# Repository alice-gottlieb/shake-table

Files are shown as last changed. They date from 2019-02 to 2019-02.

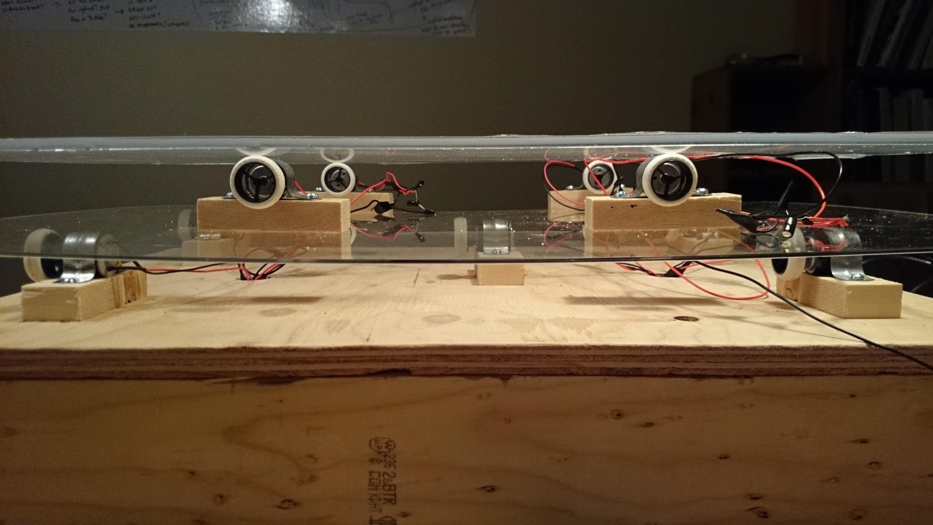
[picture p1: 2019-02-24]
picturesAndVideos/XY-FullBuild.JPG

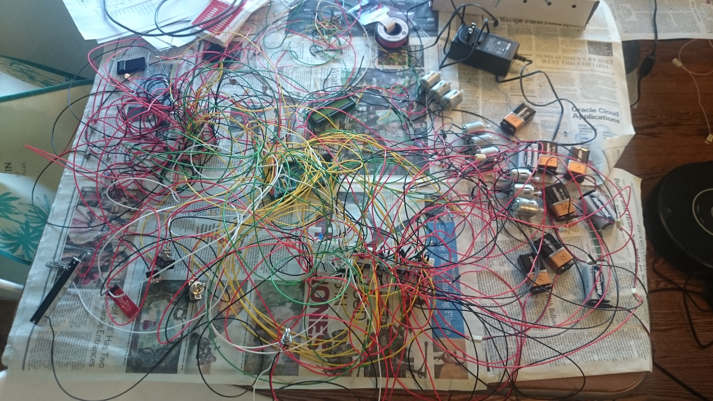
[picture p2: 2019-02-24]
picturesAndVideos/AllWiredTogether.JPG

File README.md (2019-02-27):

# shake-table
Circuit diagram and Arduino Programs to build and operate an earthquake-simulating shake table. <br>
Built using Arudino Mega 2560 Rev 3 <br>
Feature list:
* Movement in X, Y, and Z axes
* 10 DC motors
* 16 low-power vibrating motors for aftershock simulation
* Multiple potentiometers for active control of shake power 
* Readout via LCD display (not shown on circuit diagram, but supported in Arduino code), multicolored LEDs, and a variety of audio tones
* Real-time clock 
* Bluetooth connectivity

All code needed to operate shake table inside shakeTableOperationCode. Specific tests for debugging are inside testCode. Include [RTC-Lib](https://github.com/adafruit/RTClib) to operate real-time clock <br>

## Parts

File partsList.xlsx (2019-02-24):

Part Name and Quantity | URL | Unit Price | Total Price
1x Arduino Mega 2560 Rev3 Microcontroller | https://www.sparkfun.com/products/11061 | $45.95 | $45.95
17x vibration motors | https://www.sparkfun.com/products/8449 | $4.46 | $75.82
6x SN754410 H-Bridges | https://www.sparkfun.com/products/315 | $2.35 | $14.10
1x Bluetooth Mate Silver | https://www.sparkfun.com/products/12577 | $24.95 | $24.95
11x motors | https://www.sparkfun.com/products/11696 | $1.76 | $19.36
5x 9v batteries | https://www.sparkfun.com/products/10218 | $1.95 | $9.75
1x 110v AC-to-9v DC adapter | https://www.sparkfun.com/products/12889 | $5.95 | $5.95
11x 100uF capacitors | https://www.sparkfun.com/products/96 | $0.32 | $3.52
11x 10uF capacitors | https://www.sparkfun.com/products/523 | $0.41 | $4.51
4x 74HC595 SIPO Shift Registers | https://www.sparkfun.com/products/733 | $1.50 | $6.00
11x NPN BJN Transistors | https://www.sparkfun.com/products/12852 | $0.45 | $4.95
2x rotary potentiometers (linear sweep) | https://www.sparkfun.com/products/9939 | $0.95 | $1.90
2x rotary potentiometers (logarithmic sweep) | https://www.sparkfun.com/products/9940 | $0.95 | $1.90
2x linear potentiometers (linear sweep) | https://www.sparkfun.com/products/9119 | $2.95 | $5.90
1x DS1307 RTC Breakout Board | https://www.sparkfun.com/products/12708 | $14.95 | $14.95
1x resistor kit | https://www.sparkfun.com/products/10969 | $7.95 | $7.95
15x green LEDs (common cathode) | https://www.sparkfun.com/products/9650 | $0.32 | $4.80
5x blue LEDs (common cathode) | https://www.sparkfun.com/products/11372 | $0.50 | $2.50
5x red LEDs (common cathode) | https://www.sparkfun.com/products/9590 | $0.35 | $1.75
2x RGD LEDs (common cathode) | https://www.sparkfun.com/products/105 | $1.95 | $3.90
2x switches | https://www.sparkfun.com/products/9276 | $1.95 | $3.90
1x 16x2 LCD screens with RGB LED backlight | https://www.sparkfun.com/products/10862 | $14.95 | $14.95
1x assorted wires | http://www.amazon.com/Electronix-Express-Hook-Wire-Stranded/dp/B00B4ZQ3L0 | $20.00 | $20.00
2x female headers | https://www.sparkfun.com/products/115 | $1.50 | $3.00
1x storage bin | : http://www.amazon.com/Akro-Mils-20-Inch-16-Inch-Hardware-Cabinet/dp/B003P2UOCO | $26.71 | $26.71
10x 9v battery holders | https://www.sparkfun.com/products/91 | $1.13 | $11.30
 |  |  | Total:
 |  |  | $340.27

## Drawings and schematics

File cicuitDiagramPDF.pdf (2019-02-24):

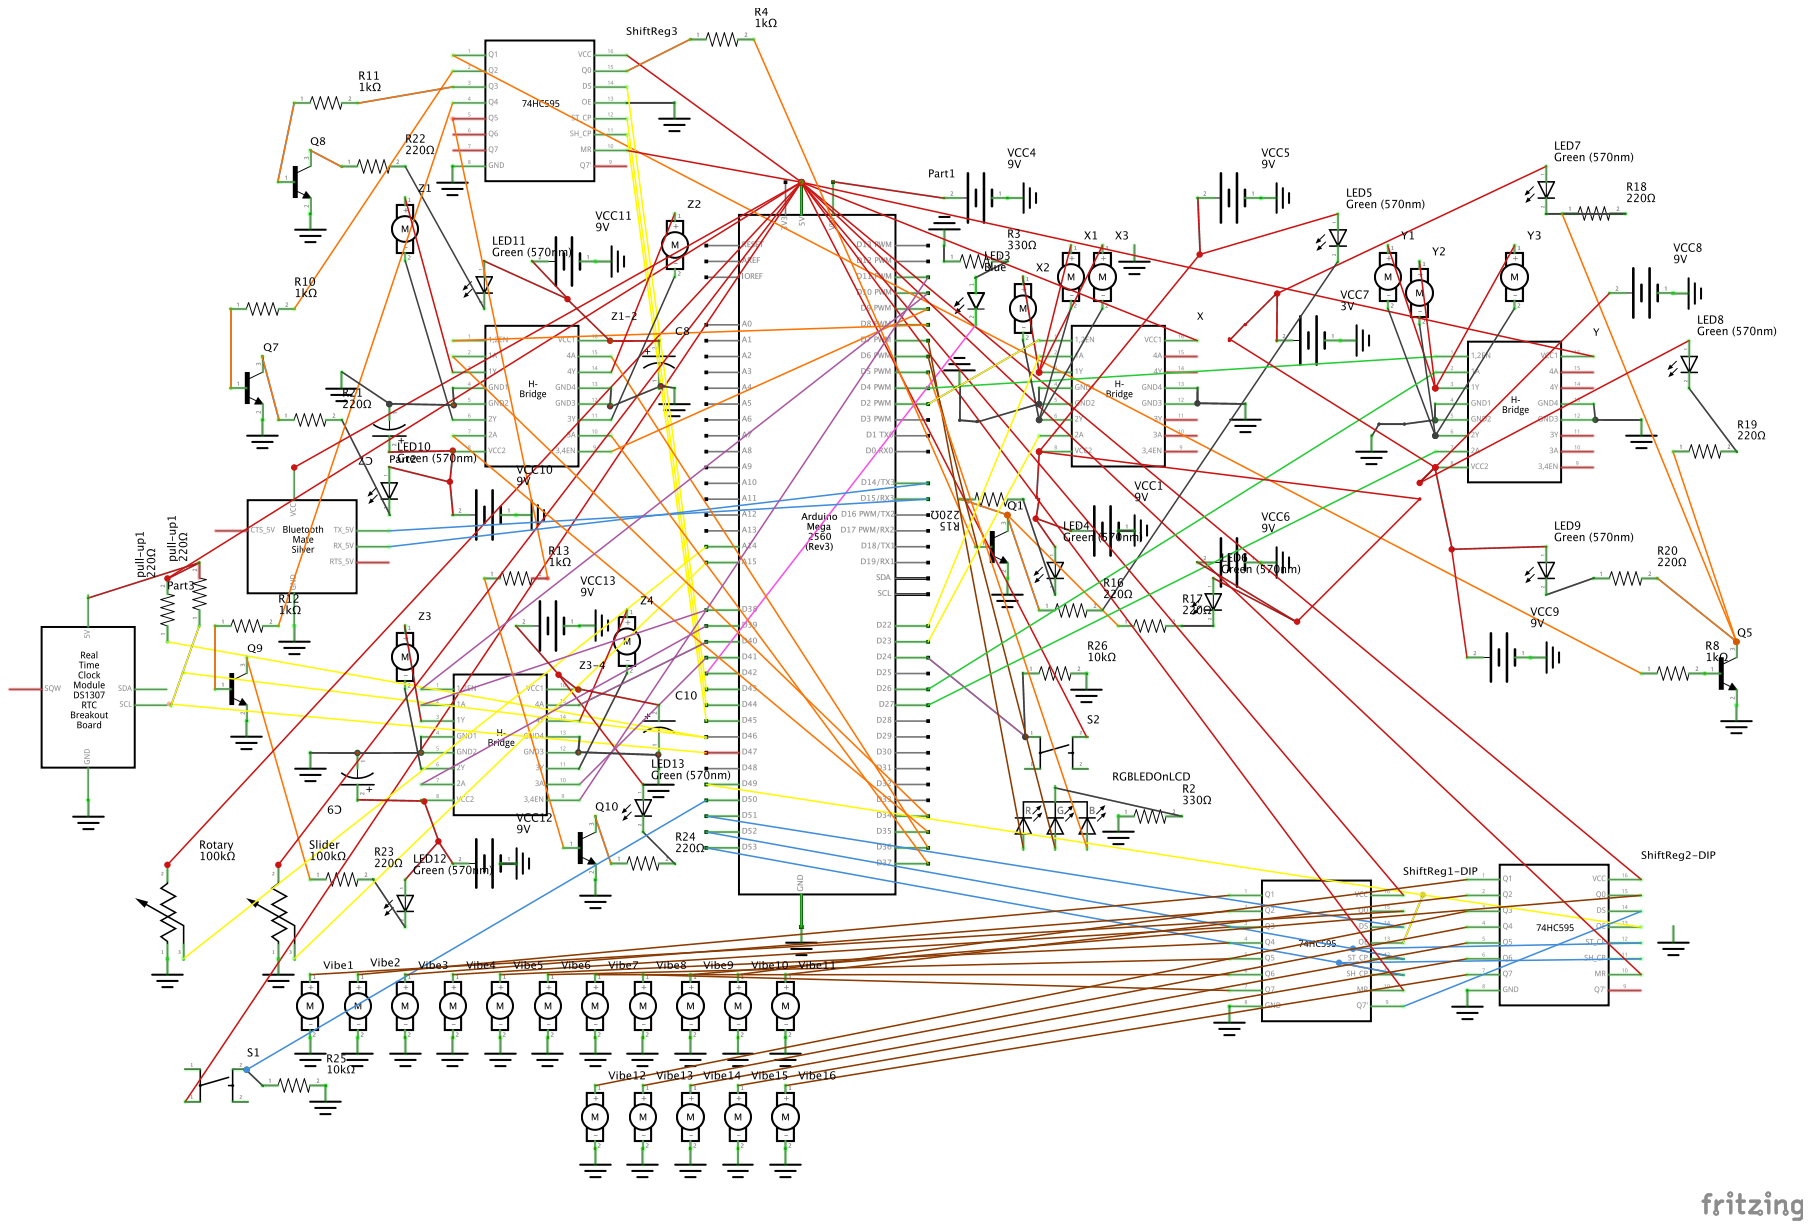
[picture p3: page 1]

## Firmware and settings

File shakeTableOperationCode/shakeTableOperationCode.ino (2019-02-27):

#include <LiquidCrystal.h>
#include <Wire.h>
//#include "RTClib.h"

/*
All functions needed to run Shake table.
Diagnostics will run automatically, other functions can be used as needed depending on settings needed.
Include RTClib to operate real-time clock
Notes:
clockwise = switch1 HIGH and switc2 LOW
countercloskwise = switch1 LOW and switch2 HIGH
clockwise is up
*/
//LiquidCrystal lcd (44, 45, 46, 47, 48, 49);
//pin numbers
byte xMotorEN = 2; //pwm
byte yMotorEN = 4; //pwm
byte z1MotorEN = 8; //pwm
byte z2MotorEN = 9; //pwm
byte z3MotorEN = 10; //pwm
byte z4MotorEN = 11; //pwm
byte lcdGreenBacklight = 12; //pwm
byte lcdRedBacklight = 13; //pwm
byte bluetoothTX = 14; //AKA TX3
byte bluetoothRX = 15; //AKA RX3
byte lcdTX = 16;
byte xMotorSwitch1  = 22;
byte xMotorSwitch2 = 23;
byte onOffSwitch = 24;
byte yMotorSwitch1 = 26;
byte yMotorSwitch2 = 27;
byte z1MotorSwitch1 = 34;
byte z1MotorSwitch2 = 35;
byte z2MotorSwitch1 = 36;
byte z2MotorSwitch2 = 37;
byte z3MotorSwitch1 = 38;
byte z3MotorSwitch2 = 39;
byte z4MotorSwitch1 = 40;
byte z4MotorSwitch2 = 41;
byte bluetoothStatusLED = 42;
byte bluetoothOnOffSwitch = 50; //digital input
byte vibeMotorShiftRegisterData = 51; //this is daisy-chained to another shift register, so there are 2 bytes of data to be sent
byte vibeMotorShiftRegisterLatch = 52;
byte vibeMotorShiftRegisterClock = 53;
byte batteryTesterShiftRegisterData = 43;
byte batteryTesterShiftRegisterLatch = 44;
byte batteryTesterShiftRegisterClock = 45;
//byte z3BatteryTester = A3;
//byte RTCData = 46;
//byte RTCClock = 47; 
//byte z4BatteryTester = A6;
byte rotaryPot = A14; //analog input
byte linearPot = A15; //analog input
//RTC_DS1307 RTC;

/*
Z  motor definitions:
motors deifind looking from behind lcd readout screen
z1Motor: bottom right corner
z2Motor: bottom left corner
z3Motor: top center
code definitions:
code 1: entire right side (z1) up, entire left side (z2) down
code 2: entire left side (z2) up, entire right side (z1) down
code 3: entire bottom side (z1, z3) up, entire top side (z2, z4) down
code 4: entire top side (z2, z4) up, entire bottom side (z1, z3) down
code 5: bottom right corner (z1) up, top left corner (z3) down
code 6: top left corner (z3) up, bottom right corner (z1) down
code 7: top right corner (z2) up, bottom left corner (z4) down
code 8: bottom left corner (z4) up, top right corner (z2) down
any other code: turns off all motors
*/

void setup(){
  //setup of pins
  for(byte pinNum = 0; pinNum < 54; pinNum++){
    pinMode(pinNum, OUTPUT);
  }
  pinMode(bluetoothOnOffSwitch, INPUT);
  pinMode(batteryTesterShiftRegisterData, OUTPUT);
  pinMode(batteryTesterShiftRegisterLatch, OUTPUT);
  pinMode(batteryTesterShiftRegisterClock, OUTPUT);
  pinMode(bluetoothRX, INPUT);
  pinMode(rotaryPot, INPUT);
  pinMode(linearPot, INPUT);
  //start LCD Display
  digitalWrite(lcdTX, HIGH);
  Serial2.begin(9600);
  delay(100);
  Serial2.write(24); //turn on w/ cursor + no blink
  Serial2.write(12); //clear
  delay(5);
  Serial2.print("Hello There!");
  Serial2.write(13); //carriage return
  /*for(int i = 0; i < 5; i++){
    DateTime dateTime = RTC.now();
    String year = String(dateTime.year(), DEC);
    String month = String(dateTime.month(), DEC);
    String day = String(dateTime.day(), DEC);
    String hour = String(dateTime.hour(), DEC);
    String minute = String(dateTime.minute(), DEC);
    String second = String(dateTime.second(), DEC);
    String date = month + "/" + day + "/" + year;
    String time = hour + ":" + minute + ":" + second;
    Serial2.print(time);
    lineErase(1);
    delay(1000);
  }*/
  Serial2.print("Diagnostics ...");
  diagnostics();
}

void loop(){
  
}

void diagnostics(){
  //lcd screen diags
  Serial2.write(12); 
  delay(5);
  Serial2.print("Diagnostics ...");
  Serial2.write(13); //cariage return
  //battery diags
  Serial2.print("Battery Diags");
  shiftOut(batteryTesterShiftRegisterData, batteryTesterShiftRegisterClock, LSBFIRST, B10000000);
  delay(500);
  shiftOut(batteryTesterShiftRegisterData, batteryTesterShiftRegisterClock, LSBFIRST, B01000000);
  delay(500);
  shiftOut(batteryTesterShiftRegisterData, batteryTesterShiftRegisterClock, LSBFIRST, B00100000);
  delay(500);
  shiftOut(batteryTesterShiftRegisterData, batteryTesterShiftRegisterClock, LSBFIRST, B00010000);
  delay(500);
  shiftOut(batteryTesterShiftRegisterData, batteryTesterShiftRegisterClock, LSBFIRST, B00001000);
  delay(500);
  shiftOut(batteryTesterShiftRegisterData, batteryTesterShiftRegisterClock, LSBFIRST, B00000100);
  delay(500);
  shiftOut(batteryTesterShiftRegisterData, batteryTesterShiftRegisterClock, LSBFIRST, B11111100);
  delay(500);
  shiftOut(batteryTesterShiftRegisterData, batteryTesterShiftRegisterClock, LSBFIRST, B00000000);
  //motor diags
  lineErase(1);
  Serial2.print("Motor Diags");
  moveXYMotors(100, true, true, 1000); //more x clockwise for 1 sec at speed 100
  moveXYMotors(100, true, false, 1000); //more x counter-clockwise for 1 sec at speed 100
  moveXYMotors(100, false, true, 1000); //more y clockwise for 1 sec at speed 100
  moveXYMotors(100, false, false, 1000); //more y counter-clockwise for 1 sec at speed 100
  /*for(byte n = 1; n <= 8; n++){ //loop through each case for Z
    moveZMotors(100, n, 1000); 
    delay(100);
  }*/
}

void moveXYMotors(double motorSpeed, boolean isX, boolean isClockwise, int time){ //speed is max 255, time is in milliseconds
  if(isX){
    if(isClockwise){
      //set to clockwise motion
      digitalWrite(xMotorSwitch1, HIGH);
      digitalWrite(xMotorSwitch2, LOW);  
    }
    else{
      //set to clockwise motion
      digitalWrite(xMotorSwitch1, LOW);
      digitalWrite(xMotorSwitch2, HIGH);  
    }
    //turn motors on
    for(int i = 0; i < 50; i++){
      analogWrite(xMotorEN, (motorSpeed*(i/50)));
      delay(time/50);
    }
    for(int i = 0; i < 50; i++){
      analogWrite(xMotorEN, (motorSpeed - (motorSpeed*(i/50))));
      delay(time/50);
    }
    //turn motors off
    analogWrite(xMotorEN, 0);
  }
    else{
    if(isClockwise){
      //set to clockwise motion
      digitalWrite(yMotorSwitch1, HIGH);
      digitalWrite(yMotorSwitch2, LOW);   
    }
    else{
      //set to clockwise motion
      digitalWrite(yMotorSwitch1, LOW);
      digitalWrite(yMotorSwitch2, HIGH);  
    }
    //turn motors on
    for(int i = 0; i < 50; i++){
      analogWrite(yMotorEN, (motorSpeed*(i/50)));
      delay(time/50);
    }
    for(int i = 0; i < 50; i++){
      analogWrite(yMotorEN, (motorSpeed - (motorSpeed*(i/50))));
      delay(time/50);
    }
    //turn motors off
    analogWrite(yMotorEN, 0);
  }
}

void moveXYMotors(double motorSpeed, boolean isX, boolean isClockwise, boolean isOn){ //speed is max 255, no time delay
  if(isOn){
    if(isX){
      if(isClockwise){
        //set to clockwise motion
        digitalWrite(xMotorSwitch1, HIGH);
        digitalWrite(xMotorSwitch2, LOW);  
      }
      else{
        //set to clockwise motion
        digitalWrite(xMotorSwitch1, LOW);
        digitalWrite(xMotorSwitch2, HIGH);   
      }
        //turn motors on
        analogWrite(xMotorEN, motorSpeed);
    }
    else{
      if(isClockwise){
        //set to clockwise motion
        digitalWrite(yMotorSwitch1, HIGH);
        digitalWrite(yMotorSwitch2, LOW);  
      }
      else{
        //set to clockwise motion
        digitalWrite(yMotorSwitch1, LOW);
        digitalWrite(yMotorSwitch2, HIGH);   
      }
      //turn motors on
      analogWrite(yMotorEN, motorSpeed);
    }
  }
  else{
    if(isX){
      analogWrite(xMotorEN, 0);
    }
    else{
      analogWrite(yMotorEN, 0);
    }
  }
}

void moveZMotors(double motorSpeed, byte code, int time){
  /*
  motor definitions:
  motors deifind looking from behind lcd readout screen
  z1Motor: bottom right corner
  z2Motor: top right corner
  z3Motor: top left corner
  z4Motor: bottom left corner
  code definitions:
  code 1: entire right side (z1, z2) up, entire left side (z3, z4) down
  code 2: entire left side (z3, z4) up, entire right side (z1, z2) down
  code 3: entire bottom side (z1, z3) up, entire top side (z2, z4) down
  code 4: entire top side (z2, z4) up, entire bottom side (z1, z3) down
  code 5: bottom right corner (z1) up, top left corner (z3) down
  code 6: top left corner (z3) up, bottom right corner (z1) down
  code 7: top right corner (z2) up, bottom left corner (z4) down
  code 8: bottom left corner (z4) up, top right corner (z2) down
  any other code: turns off all motors
  Note: clockwise turn will be up, couterclockwise will be down
  */
  
  long startingMilliseconds = millis(); //get number of milliseconds since startup
   switch(code){
     case 1: //entire right side (z1, z2) up, entire left side (z3, z4) down
       //set clockwise
       digitalWrite(z1MotorSwitch1, HIGH);
       digitalWrite(z1MotorSwitch2, LOW);  
       digitalWrite(z2MotorSwitch1, HIGH);
       digitalWrite(z2MotorSwitch2, LOW); 
       //set counterclockwise
       digitalWrite(z3MotorSwitch1, LOW); 
       digitalWrite(z3MotorSwitch2, HIGH);
       digitalWrite(z4MotorSwitch1, LOW);
       digitalWrite(z4MotorSwitch2, HIGH);
       while((millis() - startingMilliseconds) < time){ //while amount of time has not elapsed
          analogWrite(z1MotorEN, motorSpeed);
          analogWrite(z2MotorEN, motorSpeed);
          analogWrite(z3MotorEN, motorSpeed);
          analogWrite(z4MotorEN, motorSpeed);
          delay(1);
       }
       analogWrite(z1MotorEN, 0);
       analogWrite(z2MotorEN, 0);
       analogWrite(z3MotorEN, 0);
       analogWrite(z4MotorEN, 0);
       break;
     case 2: //entire left side (z3, z4) up, entire right side (z1, z2) down
        //set counterclockwise
       digitalWrite(z1MotorSwitch1, LOW);
       digitalWrite(z1MotorSwitch2, HIGH);  
       digitalWrite(z2MotorSwitch1, LOW);
       digitalWrite(z2MotorSwitch2, HIGH); 
       //set clockwise
       digitalWrite(z3MotorSwitch1, HIGH); 
       digitalWrite(z3MotorSwitch2, LOW);
       digitalWrite(z4MotorSwitch1, HIGH);
       digitalWrite(z4MotorSwitch2, LOW);
       while((millis() - startingMilliseconds) < time){ //while amount of time has not elapsed
          analogWrite(z1MotorEN, motorSpeed);
          analogWrite(z2MotorEN, motorSpeed);
          analogWrite(z3MotorEN, motorSpeed);
          analogWrite(z4MotorEN, motorSpeed);
          delay(1);
       }
       analogWrite(z1MotorEN, 0);
       analogWrite(z2MotorEN, 0);
       analogWrite(z3MotorEN, 0);
       analogWrite(z4MotorEN, 0);
       break;
     case 3: //entire bottom side (z1, z3) up, entire top side (z2, z4) down
       //set clockwise
       digitalWrite(z1MotorSwitch1, HIGH);
       digitalWrite(z1MotorSwitch2, LOW);  
       digitalWrite(z3MotorSwitch1, HIGH);
       digitalWrite(z3MotorSwitch2, LOW); 
       //set counterclockwise
       digitalWrite(z2MotorSwitch1, LOW); 
       digitalWrite(z2MotorSwitch2, HIGH);
       digitalWrite(z4MotorSwitch1, LOW);
       digitalWrite(z4MotorSwitch2, HIGH);
       while((millis() - startingMilliseconds) < time){ //while amount of time has not elapsed
          analogWrite(z1MotorEN, motorSpeed);
          analogWrite(z2MotorEN, motorSpeed);
          analogWrite(z3MotorEN, motorSpeed);
          analogWrite(z4MotorEN, motorSpeed);
          delay(1);
       }
       analogWrite(z1MotorEN, 0);
       analogWrite(z2MotorEN, 0);
       analogWrite(z3MotorEN, 0);
       analogWrite(z4MotorEN, 0);
       break;
       case 4: //entire top side (z2, z4) up, entire bottom side (z1, z3) down
                //set clockwise
         digitalWrite(z1MotorSwitch1, HIGH);
         digitalWrite(z1MotorSwitch2, LOW);  
         digitalWrite(z3MotorSwitch1, HIGH);
         digitalWrite(z3MotorSwitch2, LOW); 
         //set counterclockwise
         digitalWrite(z2MotorSwitch1, LOW); 
         digitalWrite(z2MotorSwitch2, HIGH);
         digitalWrite(z4MotorSwitch1, LOW);
         digitalWrite(z4MotorSwitch2, HIGH);
         while((millis() - startingMilliseconds) < time){ //while amount of time has not elapsed
            analogWrite(z1MotorEN, motorSpeed);
            analogWrite(z2MotorEN, motorSpeed);
            analogWrite(z3MotorEN, motorSpeed);
            analogWrite(z4MotorEN, motorSpeed);
            delay(1);
         }
         analogWrite(z1MotorEN, 0);
         analogWrite(z2MotorEN, 0);
         analogWrite(z3MotorEN, 0);
         analogWrite(z4MotorEN, 0);
         break;
       case 5: //bottom right corner (z1) up, top left corner (z3) down
         digitalWrite(z1MotorSwitch1, HIGH);
         digitalWrite(z1MotorSwitch2, LOW);
         //set counterclockwise
         digitalWrite(z3MotorSwitch1, LOW);
         digitalWrite(z3MotorSwitch2, HIGH);
                  while((millis() - startingMilliseconds) < time){ //while amount of time has not elapsed
            analogWrite(z1MotorEN, motorSpeed);
            analogWrite(z3MotorEN, motorSpeed);
            delay(1);
         }
         analogWrite(z1MotorEN, 0);
         analogWrite(z3MotorEN, 0);
         break;
       case 6: //top left corner (z3) up, bottom right corner (z1) down
         //set counterclockwise
         digitalWrite(z1MotorSwitch1, LOW);
         digitalWrite(z1MotorSwitch2, HIGH);
         //set clockwise
         digitalWrite(z3MotorSwitch1, HIGH);
         digitalWrite(z3MotorSwitch2, LOW);
         while((millis() - startingMilliseconds) < time){ //while amount of time has not elapsed
            analogWrite(z1MotorEN, motorSpeed);
            analogWrite(z3MotorEN, motorSpeed);
            delay(1);
         }
         analogWrite(z1MotorEN, 0);
         analogWrite(z3MotorEN, 0);
         break;
       case 7: //top right corner (z2) up, bottom left corner (z4) down
         //set clockwise
         digitalWrite(z2MotorSwitch1, HIGH);
         digitalWrite(z2MotorSwitch2, LOW);
         //set counterclockwise
         digitalWrite(z4MotorSwitch1, LOW);
         digitalWrite(z4MotorSwitch2, HIGH);
         while((millis() - startingMilliseconds) < time){ //while amount of time has not elapsed
            analogWrite(z2MotorEN, motorSpeed);
            analogWrite(z4MotorEN, motorSpeed);
            delay(1);
         }
         analogWrite(z2MotorEN, 0);
         analogWrite(z4MotorEN, 0);
         break;
       case 8: //bottom left corner (z4) up, top right corner (z2) down
         //set counterclockwise
         digitalWrite(z2MotorSwitch1, LOW);
         digitalWrite(z2MotorSwitch2, HIGH);
         //set clockwise
         digitalWrite(z4MotorSwitch1, HIGH);
         digitalWrite(z4MotorSwitch2, LOW);
         while((millis() - startingMilliseconds) < time){ //while amount of time has not elapsed
            analogWrite(z2MotorEN, motorSpeed);
            analogWrite(z4MotorEN, motorSpeed);
            delay(1);
         }
         analogWrite(z2MotorEN, 0);
         analogWrite(z4MotorEN, 0);
         break;
       default: //if the code is entered incorrectly, turn motors off
         analogWrite(z1MotorEN, 0);
         analogWrite(z2MotorEN, 0);
         analogWrite(z3MotorEN, 0);
         analogWrite(z4MotorEN, 0);
         break;
   }
}
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

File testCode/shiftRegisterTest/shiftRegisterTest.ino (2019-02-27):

/*
 Test of shift register to send same bits to one LCD screen as is displayed on another.
 */

byte lcdTX = 16;
byte outputEnable = 49;
byte data = 51;
byte latch = 52;
byte clock = 53;

void setup() {
  pinMode(lcdTX, OUTPUT);
  digitalWrite(lcdTX, HIGH);
  delay(100);
  Serial2.begin(9600);
  pinMode(outputEnable, OUTPUT);
  pinMode(data, OUTPUT);
  pinMode(latch, OUTPUT);
  pinMode(clock, OUTPUT);
  digitalWrite(outputEnable, LOW);
}

void loop() {
  digitalWrite(outputEnable, LOW);
  Serial2.write(17); //turn backlight on
  Serial2.write(12); //clear
  delay(5);
  Serial2.print("1");
  digitalWrite(latch, LOW);
  shiftOut(data, clock, LSBFIRST, B00000001);
  shiftOut(data, clock, LSBFIRST, B00000000);
  digitalWrite(latch, HIGH);
  delay(1000);
  Serial2.write(12); //clear
  delay(5);
  Serial2.print("2");
  digitalWrite(latch, LOW);
  shiftOut(data, clock, LSBFIRST, B00000011);
  shiftOut(data, clock, LSBFIRST, B00000000);
  digitalWrite(latch, HIGH);
  delay(1000);
  Serial2.write(12); //clear
  delay(5);
  Serial2.print("3");
  digitalWrite(latch, LOW);
  shiftOut(data, clock, LSBFIRST, B00000111);
  shiftOut(data, clock, LSBFIRST, B00000000);
  digitalWrite(latch, HIGH);
  delay(1000);
  Serial2.write(12); //clear
  delay(5);
  Serial2.print("4");
  digitalWrite(latch, LOW);
  shiftOut(data, clock, LSBFIRST, B00001111);
  shiftOut(data, clock, LSBFIRST, B00000000);
  digitalWrite(latch, HIGH);
  delay(1000);
  Serial2.write(12); //clear
  delay(5);
  Serial2.print("5");
  digitalWrite(latch, LOW);
  shiftOut(data, clock, LSBFIRST, B00011111);
  shiftOut(data, clock, LSBFIRST, B00000000);
  digitalWrite(latch, HIGH);
  delay(1000);
  Serial2.write(12); //clear
  delay(5);
  Serial2.print("6");
  digitalWrite(latch, LOW);
  shiftOut(data, clock, LSBFIRST, B00111111);
  shiftOut(data, clock, LSBFIRST, B00000000);
  digitalWrite(latch, HIGH);
  delay(1000);
  Serial2.write(12); //clear
  delay(5);
  Serial2.print("7");
  digitalWrite(latch, LOW);
  shiftOut(data, clock, LSBFIRST, B01111111);
  shiftOut(data, clock, LSBFIRST, B00000000);
  digitalWrite(latch, HIGH);
  delay(1000);
  Serial2.write(12); //clear
  delay(5);
  Serial2.print("8");
  digitalWrite(latch, LOW);
  shiftOut(data, clock, LSBFIRST, B11111111);
  shiftOut(data, clock, LSBFIRST, B00000000);
  digitalWrite(latch, HIGH);
  delay(1000);
  Serial2.write(12); //clear
  delay(5);
  Serial2.print("9");
  digitalWrite(latch, LOW);
  shiftOut(data, clock, LSBFIRST, B11111111);
  shiftOut(data, clock, LSBFIRST, B00000001);
  digitalWrite(latch, HIGH);
  delay(1000);
  Serial2.write(12); //clear
  delay(5);
  Serial2.print("10");
  digitalWrite(latch, LOW);
  shiftOut(data, clock, LSBFIRST, B11111111);
  shiftOut(data, clock, LSBFIRST, B00000011);
  digitalWrite(latch, HIGH);
  delay(1000);
  Serial2.write(12); //clear
  delay(5);
  Serial2.print("11");
  digitalWrite(latch, LOW);
  shiftOut(data, clock, LSBFIRST, B11111111);
  shiftOut(data, clock, LSBFIRST, B00000111);
  digitalWrite(latch, HIGH);
  delay(1000);
  Serial2.write(12); //clear
  delay(5);
  Serial2.print("12");
  digitalWrite(latch, LOW);
  shiftOut(data, clock, LSBFIRST, B11111111);
  shiftOut(data, clock, LSBFIRST, B00001111);
  digitalWrite(latch, HIGH);
  delay(1000);
  Serial2.write(12); //clear
  delay(5);
  Serial2.print("13");
  digitalWrite(latch, LOW);
  shiftOut(data, clock, LSBFIRST, B11111111);
  shiftOut(data, clock, LSBFIRST, B00011111);
  digitalWrite(latch, HIGH);
  delay(1000);
  Serial2.write(12); //clear
  delay(5);
  Serial2.print("14");
  digitalWrite(latch, LOW);
  shiftOut(data, clock, LSBFIRST, B11111111);
  shiftOut(data, clock, LSBFIRST, B00111111);
  digitalWrite(latch, HIGH);
  delay(1000);
  Serial2.write(12); //clear
  delay(5);
  Serial2.print("15");
  digitalWrite(latch, LOW);
  shiftOut(data, clock, LSBFIRST, B11111111);
  shiftOut(data, clock, LSBFIRST, B01111111);
  digitalWrite(latch, HIGH);
  delay(1000);
  Serial2.write(12); //clear
  delay(5);
  Serial2.print("16");
  digitalWrite(latch, LOW);
  shiftOut(data, clock, LSBFIRST, B11111111);
  shiftOut(data, clock, LSBFIRST, B11111111);
  digitalWrite(latch, HIGH);
  delay(1000);
  Serial2.write(12); //clear
  delay(5);
  Serial2.print("Everything!");
  //digitalWrite(outputEnable, HIGH);
  digitalWrite(latch, LOW);
  shiftOut(data, clock, LSBFIRST, B11111111);
  shiftOut(data, clock, LSBFIRST, B11111111);
  digitalWrite(latch, HIGH);
  delay(1000);
  digitalWrite(latch, LOW);
  shiftOut(data, clock, LSBFIRST, B00000000);
  shiftOut(data, clock, LSBFIRST, B00000000);
  digitalWrite(latch, HIGH);
  delay(1000);
}
